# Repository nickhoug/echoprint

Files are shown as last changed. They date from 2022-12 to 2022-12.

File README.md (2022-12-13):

# EchoPrint

EchoPrint is an open-source Arduino-based hardware and software system to accompany the Creality3D Ender-3 or Ender-3 Pro 3D printers to enable 3D printing for visually disabled creators. 

The EchoPrint GitHub is designed for easy screenreader navigation of the creation and usage of the EchoPrint. It is meant to accompany the Ender-3's SainSmart 3D Printer User Guide and be used with a pre-built and set-up Ender-3 printer.

This system has two components: a screen reader for the built in LCD screen and 2. 3D-Printed printer and safety guards. To reproduce the system, please refer to Quick Start [Step 0] to get started.

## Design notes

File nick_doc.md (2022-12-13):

## Communication Protocol (I2C)

Echoprint uses a common communication protocol called I2C stands for "Inter-Integrated Circuit" and basically, the controller device (the printer) sends out an address that a device connected to the printer might have. In colloquial language, the printer is mailing out a message and is first seeing if the person is home. If there is a device on the connection lines that responds to the address, then it starts to listen to the incomming transmission. This allows us to hook more than one device upto these two data lines and allows further expansion of the printer.

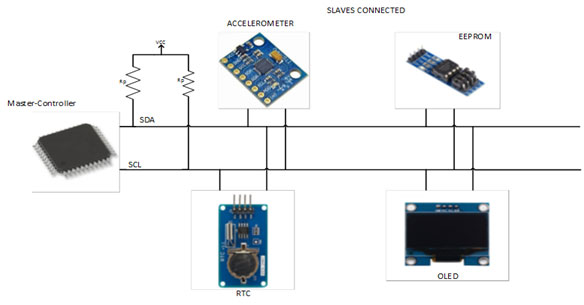
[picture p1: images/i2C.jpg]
I2C Protocol


## Text-To-Speech (tts)

The heart of this project uses Linear Predictive Coding (LPC), a speech model developed in the late 1980's and found in many kids toys at the time. If you've ever heard a dated robotic voice, it was most likely LPC that made it happen. At a high level, a model of human speech and all syllable sounds is convoluted with the input sound, thus making a computerized model of human speech. 

The  ["Talkie.h" library for Arduino ](https://github.com/ArminJo/Talkie)make use of this model and offer hundreds of vocabulary words preprogrammed into the library. The printer sends a command to Echoprint, and using a combination of the current command and the last sent command, Echoprint can determine what menu option the printer is highlighting. Once it knows the menu item in question, the specific word or set of words is sent to the speakers so the user can hear the item. 

There are some ways to preprogram your own words, and even a couple tools including BlueWizard for MacOS and the "python_wizard" available on the Talkie.h Github, but we found the preprogrammed words to be sufficient enough and expansion is definetly available in the future. 

## How to Install Echoprint

### 1. Remove the mainboard cover

Located on the bottom of the printer are three hex screws that utilize a size 2mm hex allen wrench. Remove these screws and gain acess to the main motherboard of the printer. Keep these screws somewhere save and when the cover comes off, there will be a fan cable attached to it, so disconnect it carefully. 

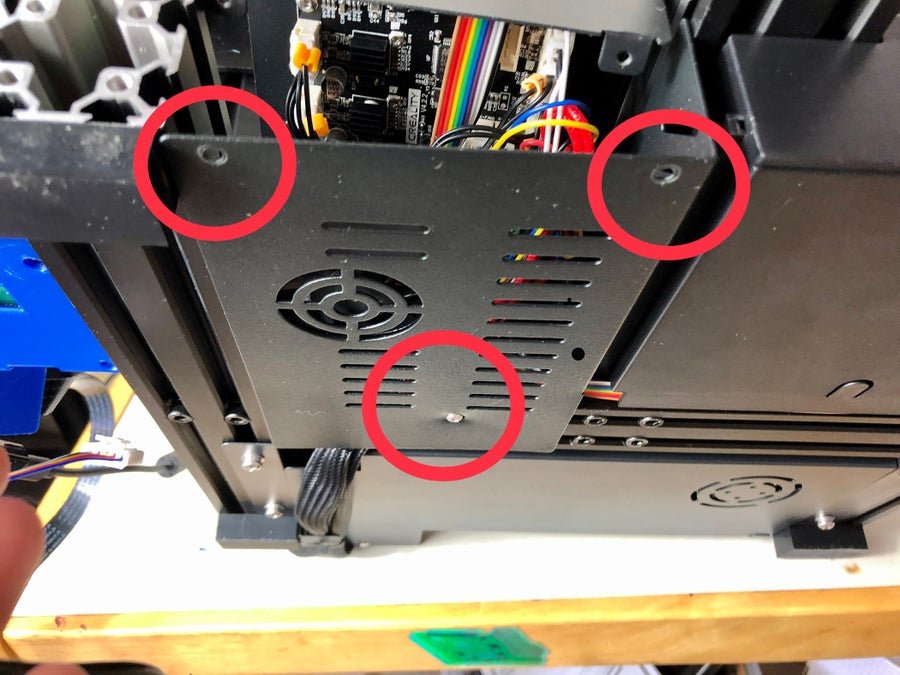
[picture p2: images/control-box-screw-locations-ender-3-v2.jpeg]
Mainboard Cover


### 2 Install the bootloader for the Creality Ender 3 Pro

Before any code can be flashed onto the printer, the bootloader needs to be installed first. This allows the printer to run any code put on to it and configures all of the internal settings. The best method for this is following along with the video below. This is a simple process that is necessary for programming the printer for a variety of applications, not just Echoprint. 

Hardware Required: 
- [AVR USB ISP Programmer](https://www.amazon.com/dp/B07NZ59VK2?psc=1&ref=ppx_yo2ov_dt_b_product_details)
- [3x2 6-pin Ribbon Cables](https://www.amazon.com/dp/B07Q2SX5CX?psc=1&ref=ppx_yo2ov_dt_b_product_details)

Video:  

IMAGE_ALT (https://www.youtube.com/watch?v=aquuSNEekvY)

### 3. Download the repository from the [Echoprint Github](https://github.com/nickhoug/echoprint)

This repository holds everything from documentation to the Ender 3 CAD files for all of the mechanical parts. Most importantly is the directory: 
    
    echoprint/Ender-3 Firmware (Marlin)/Ender-3 (includes power failure resume- English)/Marlin/Marlin.ino

This is the Arduino source code for the Ender 3 Pro and includes the Echoprint library files within the parent directory "Marlin", plus all of the instances of where the functions need to be called. Mainly, these functions are congregated in the "ultralcd.cpp" file. 

### 4. Remove the circuit board from the printer. 

Around and within the circuit board are 6 hex screws that utilize the same screwdriver as before. Remove these screws and keep them somewhere save - they are all the same size. 

After this is done, disconnect all of the connections to the printer. It's intuitive where they go and they are all labeled, but make sure to take lots of pictures as you go. The goal is to remove the board and prepare it for soldering, so we need access to the other side. 

### 5. Solder and splice the necesary connections onto the Ender 3 mainboard. 

Now that we have the software downloaded, we now need to establish an I2C connection. Through the use of Pin 27 and Pin 29 on the Ender 3 mainboard. The mainboard is very short of GPIO pins, so were going to have to hack it to make it work. 

First off is pin 27. This is a forgotton GPIO pin located under one of the boards main capacitors. The story behind this was that there was a connector for it to expand the printers hardware, but due to heating issues, this connector was removed and a capacitor was put in it's place. Located as shown in the picture below (this is from a dated source, and back then, it was still called pin 35). Make sure to cover with either heat shrink or electrical tape.

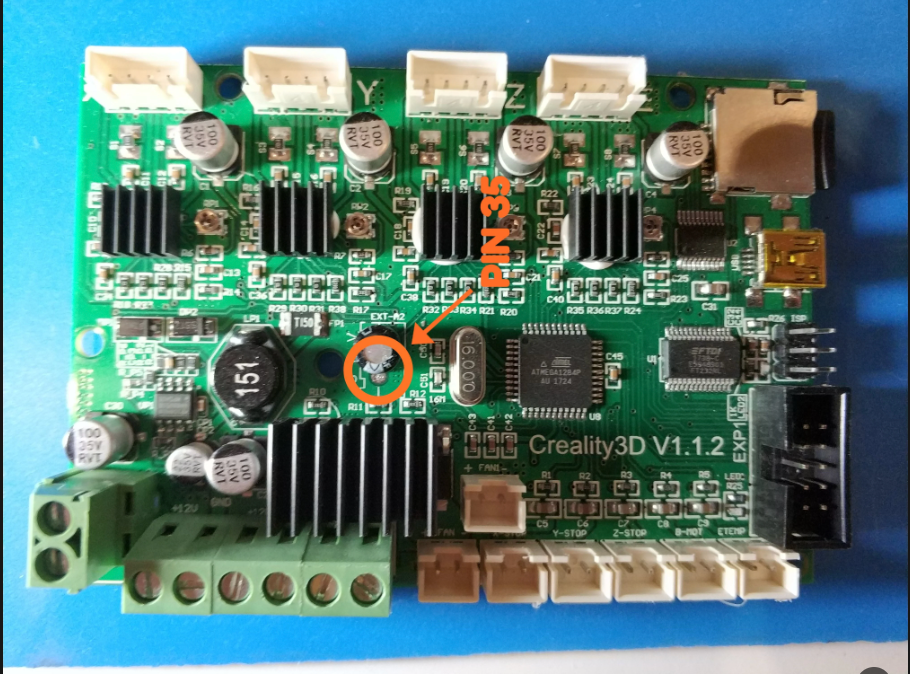
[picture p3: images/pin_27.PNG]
Pin 27


To get access to the pin, the solder needs to be removed from the hole and a jumper/wire needs to be resoldered in it's place. For the Echoprint application, a male jumper with a female end thats around 8 inches long is recommended.

Next up is pin 29. This pin is connected to the buzzer located on the LCD screen for the printer and to gain access, we need to splice into it using the rainbow ribbon connector on the printer. There are adapters made for this pin, but splicing into the wire works just as well. it is important to note that this will **remove buzzer functionality**. The engineering choice made here was that if exterrnal speakers were being added to the printer, the haptic feedback buzzer was worth ditching. On the rainbow LCD connector, the one that plugs into the black 2x5 connector near the USB port, cut the **brown** wire about an inch from the connection. Pull this wire away from the rest of the ribbon cable and solder another female jumper to it, again 8 inches in length. Again, make sure to cover with either heat shrink or electrical tape. 

### 6. Add power and ground lines 

Now that the data lines are established, we now need power and ground. In between the 2x5 LCD display connectopr and the USB is a 3x2 header pin connector. On the side closest to the edgeof the PCB and in the orientation as shown in the picture above, the pin closest to the USB port is the Ground pin and the pin closest to the LCD connector is the Power pin, skipping the one in the middle. Connect female-to-female jumpers to these pins and make sure the connections are about 8 inches long. 

### 7. Reinstallation

Once these two connections are made, reinstall the mainboard following the reverse steps as before and route the connections threw the small notch in the top plate; the plate the board is mounted to. Make sure to mount the bottom cover and fan back to the board and plugging it in the process. 

### 8. Mount Echoprint

Now that all of the electrical connections are made, we can start mounting the Echoprint system. Uncover the Echoprint system and locate the header pins. Using the schematic below, wire up all the connections, route it through the routing hole at the top of the box, and recover Echoprint. 

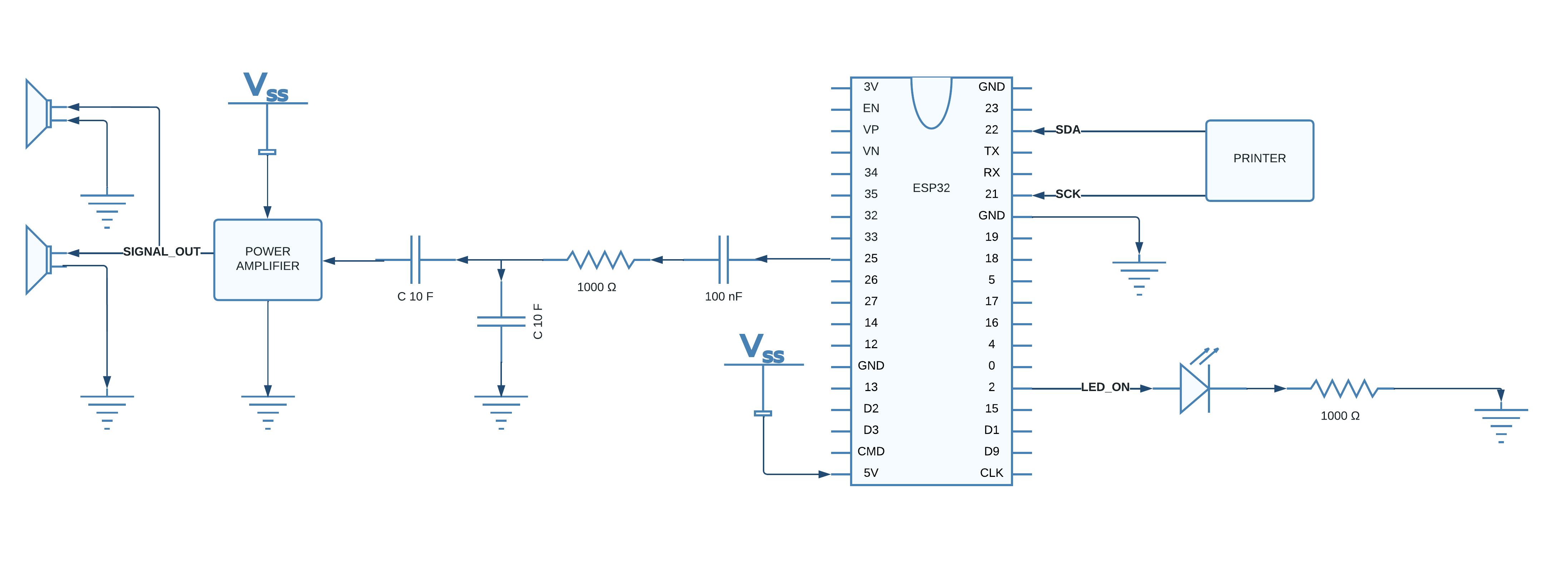
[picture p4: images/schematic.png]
Schematic


With the printer's LCD facing you, on the bottom right are 2 M4 screws. Unscrew these and thread them through the cooresponding holes on the Echoprint mount. Screw the screws back in to the holes they came out of and the Echoprint system is mounted. 

### 9. Finish

After this, Echoprint should power on with your printer and using 1980's text-to-speech technology, read out the LCD on the Ender 3 Pro. 

Given that the Creality Ender 3 system is an open-source system likely to experience updates in it's time, the following menu was used to program Echoprint and update files will be posted on the Github. 

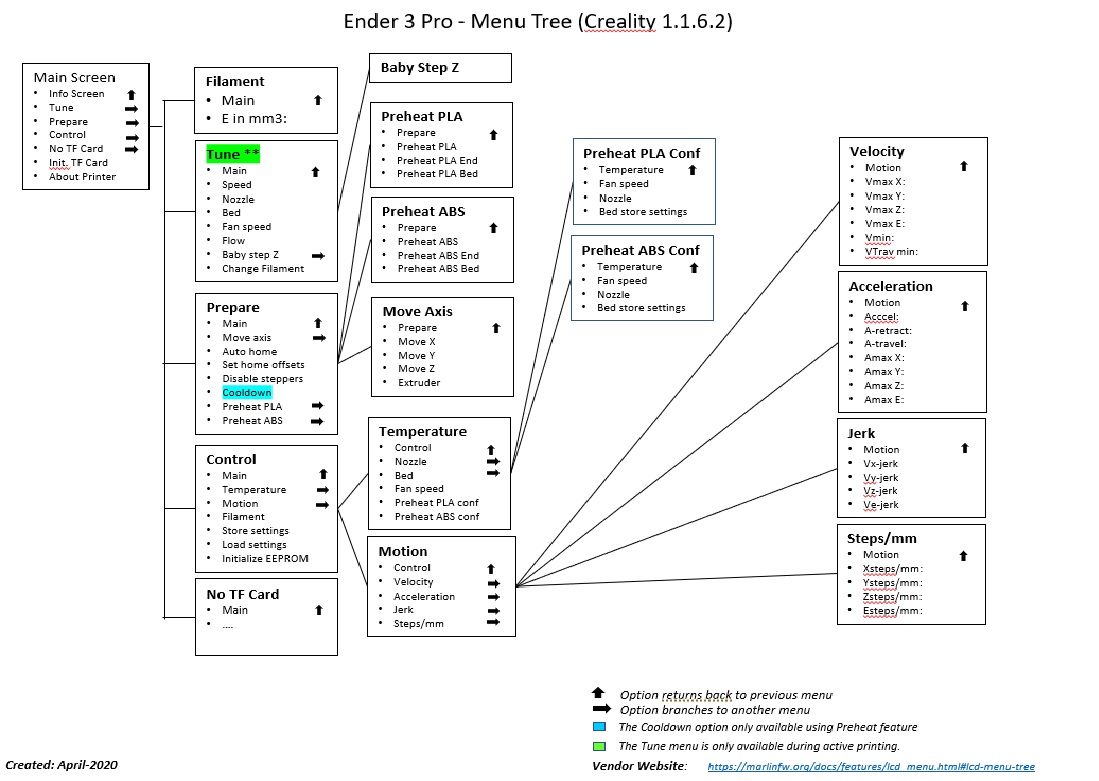
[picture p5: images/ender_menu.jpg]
Menu Tree


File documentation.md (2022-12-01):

# EchoPrint Documentation

## Abstract

EchoPrint is an Arduino-based hardware system for the Ender 3 and Ender 3 Pro 3D printers. This system is meant to act as a screen reader for the built in LCD screen on the printer. 
 
## How to Use 

## Features 

### Hardware/Firmware

## Things to do for documentation
- Make schematic 
- Outline how bigbanging system works
- List hardware pieces
- Talk about main problem and Lindsay? 
- Link Github 
- Make block diagram 
- Outline how to use the system
-

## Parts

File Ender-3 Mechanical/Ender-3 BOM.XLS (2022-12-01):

Ender-3 BOM
Part Code | Part Name | Specification | UNIT | Qty
200101027 | Control panel | 1284P | PCS | 1
200102010 | LCD |  | PCS | 1
400101002 | E plate | 2.5mm | PCS | 1
400101005 | Y Motor holder | 3mm | PCS | 1
400101006 | X Adjustment Block | 3mm | PCS | 1
400101027 | Z Stent | 3.0mm | PCS | 1
400101029 | Fan cover | 0.8mm | PCS | 1
400101081 | Support frame | 2.0mm | PCS | 1
400101103 | E motor bracket | 2.5mm，B1 | PCS | 1
400101104 | X motor bracket | 3mm，B1 | PCS | 1
400101130 | Sheetmetal enclosure bottom | 0.8MM | PCS | 1
400101131 | Sheetmetal enclosure top | 0.8MM | PCS | 1
400101133 | LCD support | 2MM | PCS | 1
400101007 | Y Adjustment Block | 3mm | PCS | 1
400101129 | Y plate | 4mm | PCS | 1
400102065 | 2020 Top Profile | 20*20-L330 | PCS | 1
400102066 | 2020 X Profile | 20*20-L345 | PCS | 1
400102067 | 2040 Y Profile | 20*40-L330 | PCS | 1
400102068 | 2040 Right Profile | 20*40-L400 | PCS | 1
400102069 | 2040 Left Profile | 20*40-L400 | PCS | 1
400102070 | 4040 Central Profile | 40*40-L250 | PCS | 1
400102071 | 4040 Left Profile | 40*40-L290 | PCS | 1
400102072 | 4040 Right Profile | 40*40-L290-2 | PCS | 1
400103001 | E gear | D11-40 | PCS | 1
400104004 | Heat block | 20*20*10 | PCS | 1
400105008 | Radiator | 12*20*27.8mm,2*M3 | PCS | 1
400106003 | nozzle | 0.4mm | PCS | 2
400107006 | Catheter | D7-M6-L28mm | PCS | 1
400108001 | Spacers for rollers | D8-d5-H-8.35mm | PCS | 11
400108002 | Eccentric column | D7.2-d5-H-8.35mm | PCS | 5
400201001 | 42-34 Motor | JK42HS34-0844YA-03F | PCS | 3
400201004 | 42-40 Motor | JK42HS40-1004AC-01F | PCS | 1
400202002 | 624U Pillow | 624U | PCS | 1
400202003 | F688ZZ Pillow | F688ZZ | PCS | 4
400202004 | 625ZZ Pillow | 625ZZ | PCS | 26
400204002 | Extrusion Spring | 1.1*8*L22 | PCS | 5
400205002 | M2*8 Socket Head Screw | M2*8 | PCS | 2
400205003 | M2*10 Socket Head Screw | M2*10 | PCS | 2
400205007 | M3*18 Socket Head Screw | M3*18 | PCS | 1
400205013 | M4*8Socket Head Screw | M4*8 | PCS | 7
400205014 | M4*10 Socket Head Screw | M4*10 | PCS | 2
400205015 | M4*16 Socket Head Screw | M4*16 | PCS | 4
400205018 | M3*3 screw | M3*3 | PCS | 4
400205019 | M4 screw | M4 | PCS | 4
400205021 | M3*4 Pan Head Screw | M3*4 | PCS | 1
400205029 | M3*6 Pan Head Screw | M3*6 | PCS | 18
400205031 | M3*10 Pan Head Screw | M3*10 | PCS | 12
400205032 | M3*16 Pan Head Screw | M3*16 | PCS | 5
400205044 | M5*8 Pan Head Screw | M5*8 | PCS | 8
400205053 | M5*30 Pan Head Screw | M5*30 | PCS | 10
400205055 | M5*40 Pan Head Screw | M5*40 | PCS | 3
400205060 | M3*10 Pan Head Screw | M3*10-P | PCS | 1
400205068 | M4*14 Pan Head Screw | M4*14-P | PCS | 2
400205074 | M4*35 Flush Head Screw | M4*35-P | PCS | 4
400205097 | M5 Self-locking nut | M5 | PCS | 13
400205098 | M8 Self-locking nut | M8 | PCS | 2
400205101 | M4 T-Slot Nut | M4T | PCS | 8
400205102 | M5 T-Slot Nut | M5T | PCS | 3
400205105 | M3 Split Washer | M3 | PCS | 6
400205106 | M4 Split Washer | M4 | PCS | 7
400205107 | M5 Split Washer | M5 | PCS | 12
400205109 | M5 washer | M5 | PCS | 5
400205110 | M5 washer1 | 5*8*1 | PCS | 13
400205111 | z nut | T8*8 | PCS | 1
400205122 | M4*20 Socket Head Screw | M4*20 | PCS | 3
400205140 | M4*18 Pan Head Screw | M4*18-P | PCS | 2
400205141 | M3*40 Pan Head Screw | M3*40-P | PCS | 4
400205144 | M3*18 Pan Head Screw | M3*18-P | PCS | 2
400205148 | M4*16 Screw |  | PCS | 5
400205153 | M3*6 Screw | M3*6 | PCS | 2
400205163 | M5*25 Socket Head Screw | M5*25 | PCS | 6
400205165 | M5*40 Socket Head Screw | M5*40 | PCS | 2
400205166 | M5*45 Socket Head Screw | M5*45 | PCS | 10
400205176 | M8*35 Pan Head Screw | M8*35 | PCS | 2
400206017 | Z threaded rod | T8*8-L365mm | PCS | 1
400208004 | Z coupler | D5*8 | PCS | 1
400210001 | Pneumatic joint | D4M8 | PCS | 1
400210002 | M6 Pneumatic joint | KJH04-06 | PCS | 2
400211009 | 2GT-pulley | 2GT-d5-20-6mm | PCS | 2
400212037 | X belt | 2M-W6-L786mm | PCS | 1
400212038 | Y belt | 2M-W6-L743mm | PCS | 1
400214001 | Copper cover | D8-0.8 | PCS | 4
400301008 | 24V15A power supply | 24V 15A | PCS | 1
400302026 | Hot bed | 24V，235*235mm，220W | PCS | 1
400303006 | Nozzle thermistor | D1.8-L1000mm-100K | PCS | 1
400303022 | Bed thermistor | D1.8-L700mm-100K | PCS | 1
400304001 | limit switch | 3PIN | PCS | 3
400305007 | power switch | 10A | PCS | 1
400306127 | Red silicone wire | 16号-L170mm | PCS | 1
400306128 | Yellow silicone wire | 18号-L170mm | PCS | 1
400306145 | Black silicone wire | 16号-L170mm | PCS | 1
400306217 | Hot bed line | 16号-L500mm | PCS | 1
400306221 | Red silicone wire | 16号-L90mm, | PCS | 1
400306222 | Main board line | 16号-L310mm,XT60 | PCS | 1
400306223 | power line | 16号-L170mm,XT60 | PCS | 1
400306224 | X,E Motor Line | Motor Line L670mm，Limit Line L750mm | PCS | 1
400306225 | Y Motor Line | L420mm | PCS | 1
400306226 | Z Motor Line | Motor LineL280mm，Limit Line L180mm | PCS | 1
400306228 | Display line | 10pin,L470mm | PCS | 1
400307001 | lcd Knob |  | PCS | 1
400308002 | Heater | 24V，40W-L1000MM，Φ6*20 | PCS | 1
400309032 | Cold section fan | 24V-4010-L1000-7600r | PCS | 1
400309044 | Nozzle fan | 24V-4010-L1000-5800r | PCS | 1
400309045 | Case fan | 24V-4010-L150mm | PCS | 1
400402010 | Z motor bracket |  | PCS | 1
400402020 | 2020 Endcap | 2020 | PCS | 2
400402023 | Nozzle fan duct |  | PCS | 1
400402028 | Power holder | 2mm | PCS | 1
400402032 | Y limit switch bracket | ABS | PCS | 1
400402033 | Z limit switch bracket | ABS | PCS | 1
400403003 | Rollers |  | PCS | 13
400403004 | Support tube |  | PCS | 1
400403005 | M30 Plastic nut | M30*6.5 | PCS | 2
400404030 | Hot bed wire bracket |  | PCS | 1
400404031 | Hot bed line support cover |  | PCS | 1
400404032 | E idler tensioner |  | PCS | 1
400404033 | E housing |  | PCS | 1
400404038 | X limit switch bracket | ABS | PCS | 1
400404040 | Hand Twisted Nut | D60mm | PCS | 4
400404041 | 4040 Endcap | ABS | PCS | 2
400406006 | Foot pads | 20*40mm*3mm | PCS | 4
400407013 | D4 Teflon tube | D4-d2-L400mm | PCS | 1
400409003 | Silk pole cover | T8*8 | PCS | 1
400501034 | Linear tube | W8-L450mm | PCS | 1
400501035 | Linear tube | W8-L950mm | PCS | 1
400504007 | Fan cover sticker |  | PCS | 1
400504008 | Product Qualification Certificate |  | PCS | 1
400505021 | Fiber board | 235*235*1.0mm | PCS | 1
400506001 | Scissor |  | PCS | 1
400506002 | shovel |  | PCS | 1
400506005 | 1.5# Hexagonal wrench inside |  | PCS | 1
400506006 | 2# Hexagonal wrench inside |  | PCS | 1
400506007 | 2.5# Hexagonal wrench inside |  | PCS | 1
400506008 | 3# Hexagonal wrench inside |  | PCS | 1
400506009 | 4# Hexagonal wrench inside |  | PCS | 1
400506011 | screwdriver |  | PCS | 1
400506016 | power cord |  | PCS | 1
400506020 | needle |  | PCS | 1
400506029 | tie | 4*150mm | PCS | 10
400506035 | 6# Open wrench |  | PCS | 1
400506036 | 8-10# Open wrench |  | PCS | 1
400506044 | Clip | 6#,15mm | PCS | 4
500101065 | Bubble cotton | 495*380*160mm | PCS | 1
500201001 | Self-Sealing bag | 6cm*9cm*0.8mm | PCS | 14
500201002 | Self-Sealing bag | 9cm*13cm*0.8mm | PCS | 1
500201004 | Self-Sealing bag | 15cm*20cm*0.8mm | PCS | 2
500201006 | Self-Sealing bag | 18cm*26cm*0.6mm | PCS | 1
500201008 | Prevention electrostatic bag | 15cm*20cm | PCS | 1
500301056 | paper box | 510*400*190mm | PCS | 1
500601001 | Opinion Card |  | PCS | 1
600101011 | Instruction |  | PCS | 1
600401004 | Memory Card | 8G | PCS | 1
600501001 | Card Reader |  | PCS | 1
600601016 | warranty card |  | PCS | 1
600601023 | Manufacture of numbered stickers | 60*10.4MM | PCS | 1
600601026 | Specification stickers | 65*40mm | PCS | 1
600601058 | Facebook code sticker | 41*41mm | PCS | 1
700206003 | Testing consumables | 5M | PCS | 1
700301044 | High temperature cotton | 20*50mm | PCS | 1
700301051 | gummed paper | 30*60 | PCS | 3
700301054 | gummed paper | 60*60mm | PCS | 1
700301056 | High temperature cotton | 50*60mm | PCS | 1

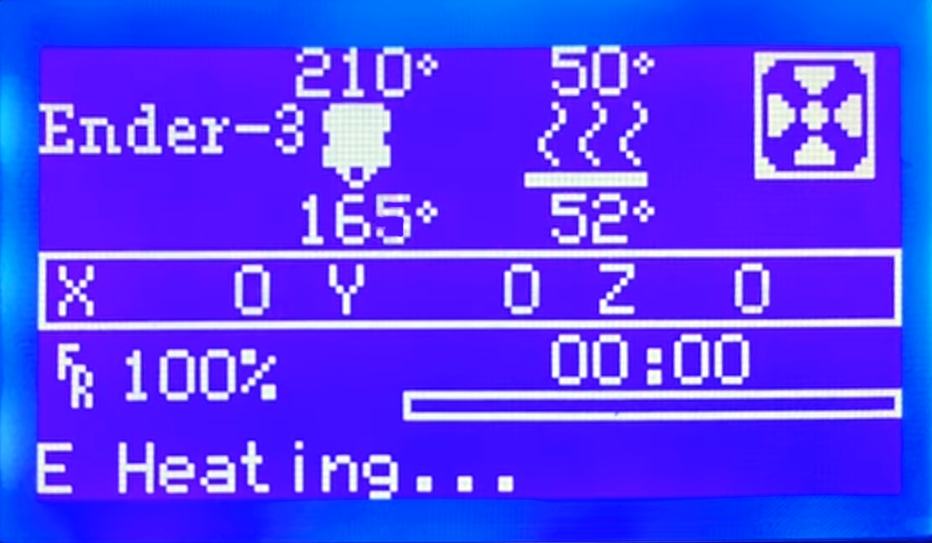
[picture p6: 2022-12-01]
Ender-3 Mechanical/Ender-3 Parts/ender_lcd.png

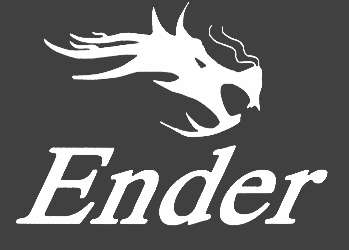
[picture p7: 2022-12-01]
Ender-3 Mechanical/Ender-3 Parts/ender-3.png

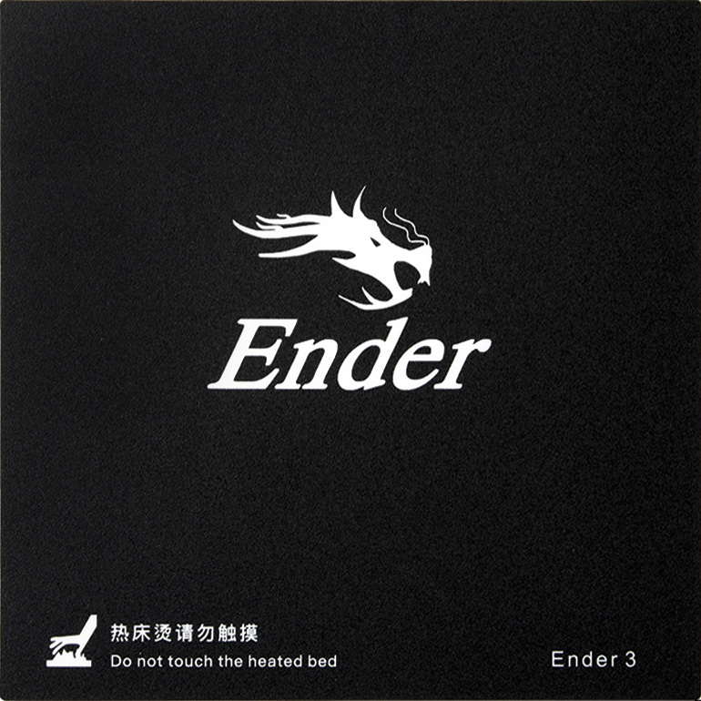
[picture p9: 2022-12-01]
Ender-3 Mechanical/Ender-3 Parts/ender-3.jpg

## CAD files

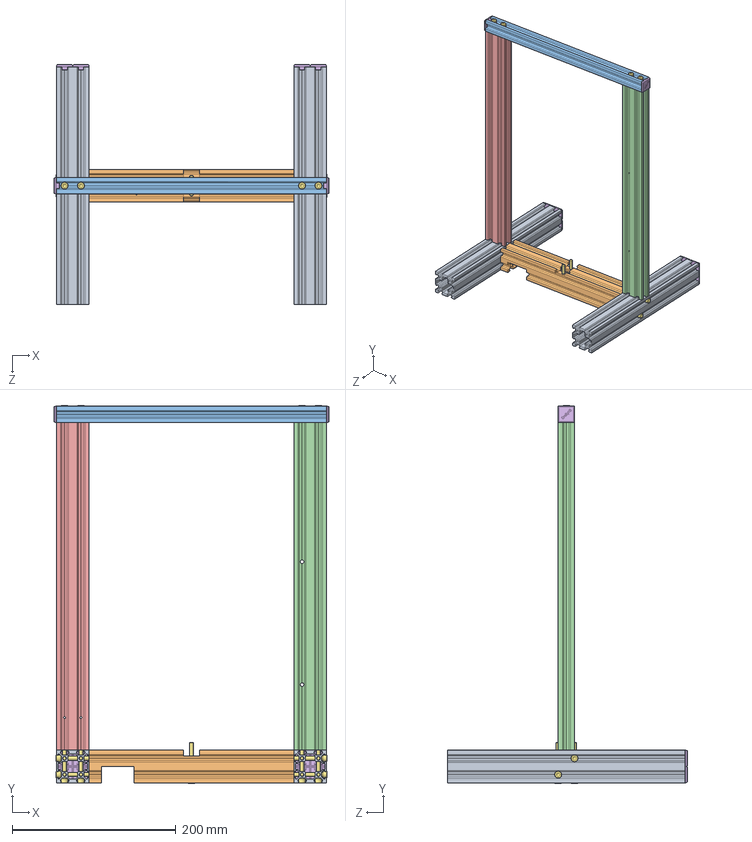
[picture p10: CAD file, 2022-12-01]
Ender-3 Mechanical/Ender-3 Parts/ASM Frame.SLDASM
335.7 x 461.6 x 292.9 mm
4040 profile x 2
4040-3 profile
2020-2 profile
2040-3R profile
2040-3L profile
2020 Endcap x 10
M5X45 Socket Head Screw x 14

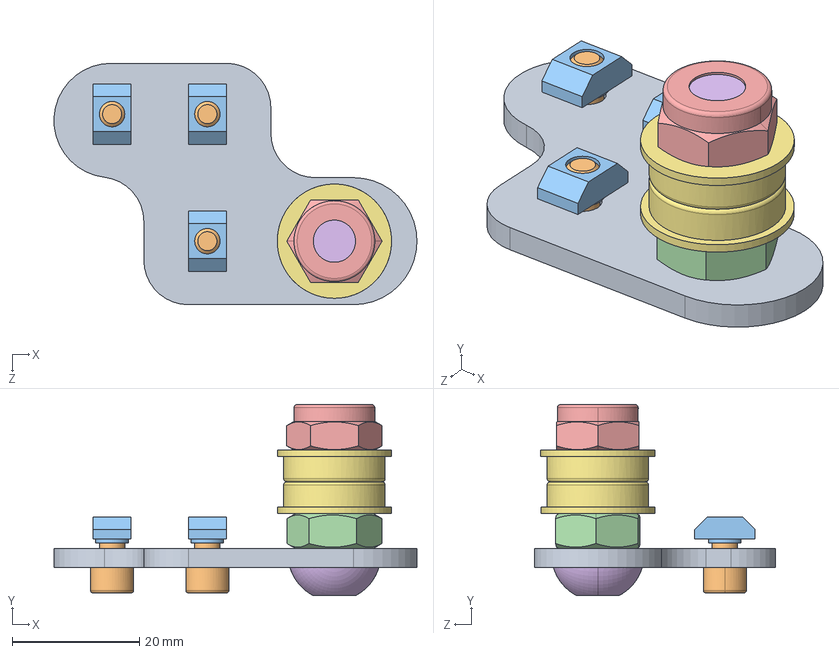
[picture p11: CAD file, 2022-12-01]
Ender-3 Mechanical/Ender-3 Parts/pulley mount.SLDASM
57.1 x 30.1 x 38.0 mm
Y Adjustment Block
M4X8 Socket Head Screw x 3
M4 T-Slot Nut x 3
M8 nut
M8 Self-locking nut
M8X25 Pan Head Screw
F688 pillow x 2

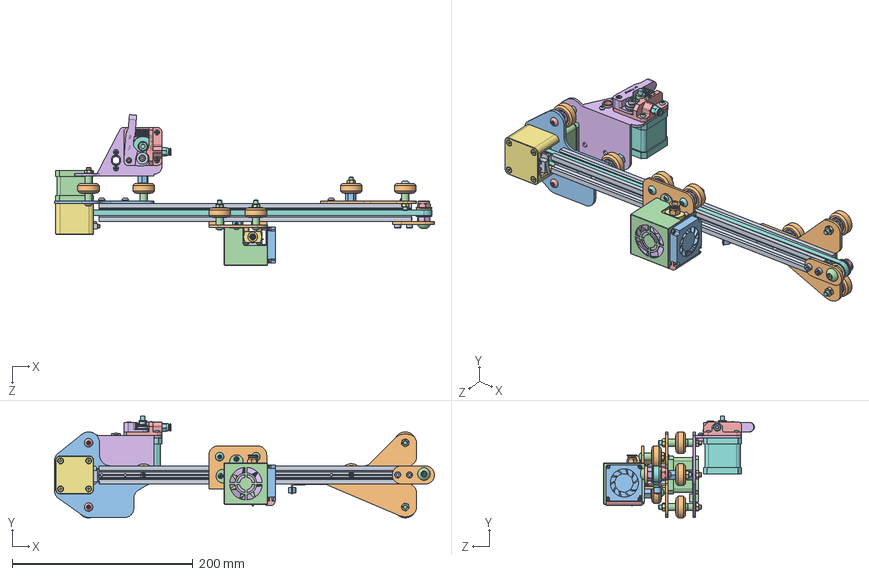
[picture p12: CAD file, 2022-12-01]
Ender-3 Mechanical/Ender-3 Parts/ASM X-Axis.SLDASM
420.0 x 112.6 x 166.7 mm
2020 profile
Z Stent
X motor bracket
42-34 motor
z nut
E motor bracket
X limit switch bracket
X belt
limit switch
2GT-pulley
Copper cover x 2
M4 Split Washer x 5
M3 Split Washer x 4
M4X16 Pan Head Screw x 4
M3X40-P x 4
M3X10 Pan Head Screw x 8
M3X6Pan Head Screw x 4
Rollers x 9
Eccentric column x 3
Spacers for rollers x 9
M5X40 Pan Head Screw x 3
625pillow x 18
M5 Self-locking nut x 9
40-42 motor
624U pillow
M3X18 Socket Head Screw
Extrusion Spring
E gear
E housing 2
E idler tensioner
M3X10 Flush Head Screw
M6 Pneumatic joint
M4X8 Socket Head Screw x 3
X Adjustment Block
M5 T-Slot Nut x 2
M8X25 Pan Head Screw
M8 Self-locking nut
M8 nut
F688 pillow x 2
M5X30 Pan Head Screw x 6
M5 Split Washer
E plate
Cold section fan
Fan cover
Nozzle fan duct
Nozzle fan
Radiator
nozzle
Heat block
Pneumatic joint
Nozzle thermistor
Heater
M3X16 Pan Head Screw x 2
M3×18 Flush Head Screw x 2
M3 Screw x 2
M5 washer
M2X8 Socket Head Screw x 4

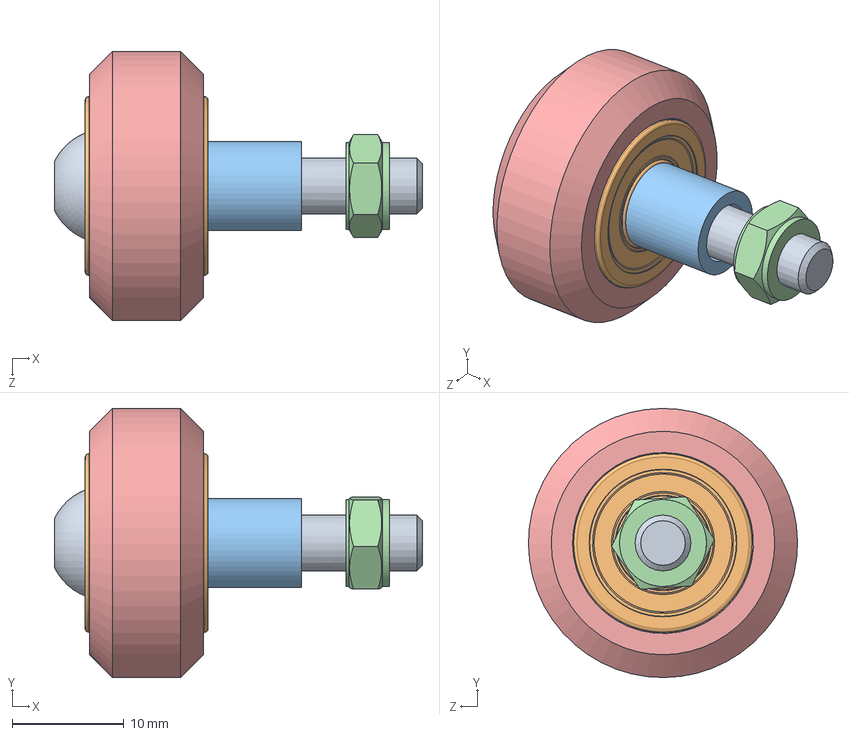
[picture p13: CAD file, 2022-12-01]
Ender-3 Mechanical/Ender-3 Parts/ASM Roller Y-Axis.SLDASM
33.0 x 24.1 x 24.1 mm
M5X30 Pan Head Screw
625pillow x 2
Spacers for rollers
M5 Self-locking nut
Rollers

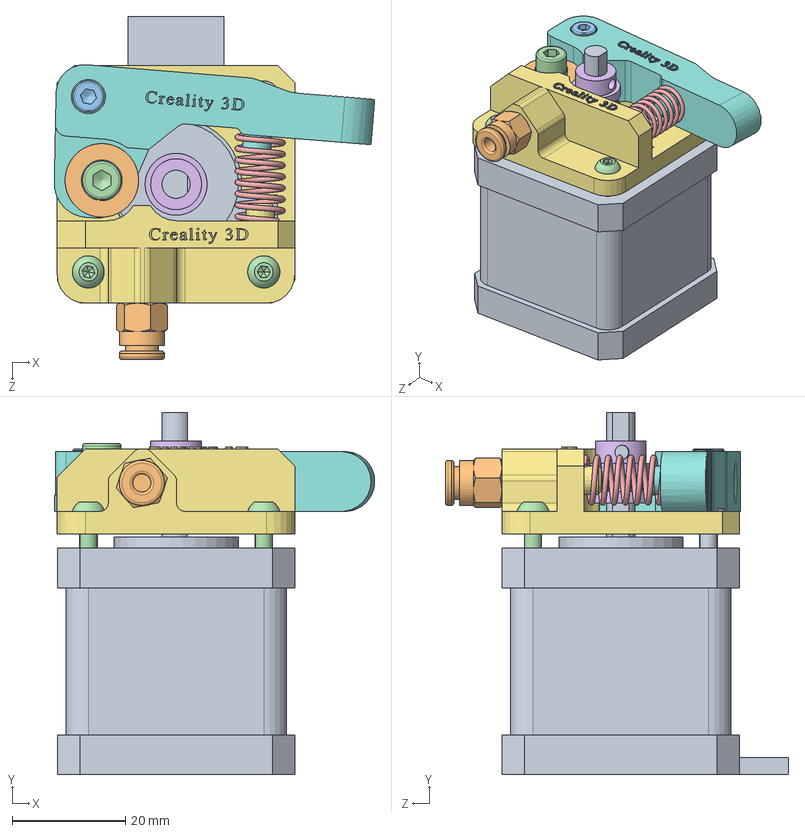
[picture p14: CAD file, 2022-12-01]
Ender-3 Mechanical/Ender-3 Parts/ASM Extruder.SLDASM
56.7 x 64.0 x 60.7 mm
40-42 motor
624U pillow
M3X18 Socket Head Screw
M3X10 Pan Head Screw x 2
Extrusion Spring
E gear
E housing 2
E idler tensioner
M3X10 Flush Head Screw
M6 Pneumatic joint
M4 Split Washer
M4X8 Socket Head Screw

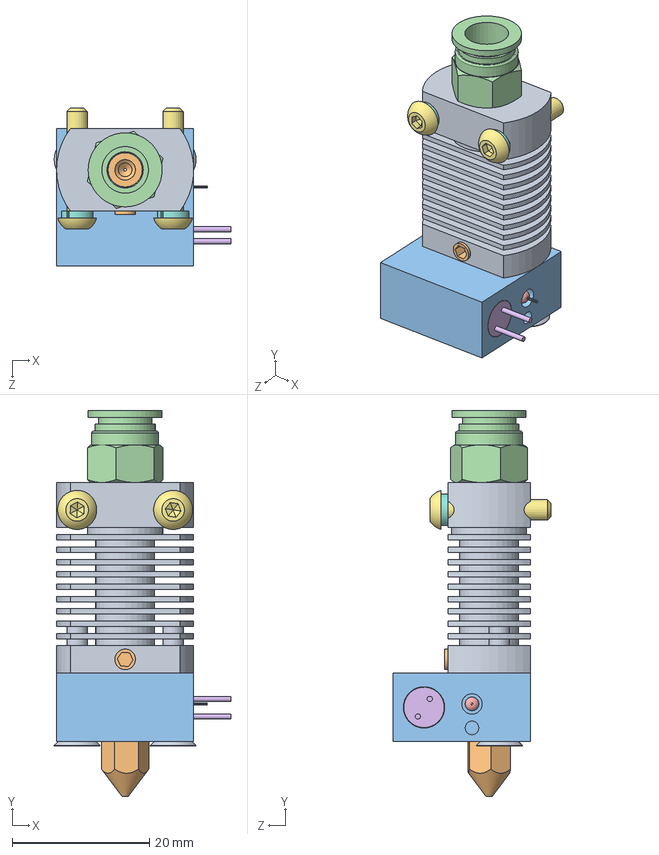
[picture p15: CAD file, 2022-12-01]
Ender-3 Mechanical/Ender-3 Parts/ASM Heating Unit.SLDASM
25.8 x 56.3 x 23.0 mm
Radiator
nozzle
Heat block
Pneumatic joint
Nozzle thermistor
Heater
M3X16 Pan Head Screw x 2
M3 Split Washer x 2
M3×18 Flush Head Screw x 2
M3 Screw x 2

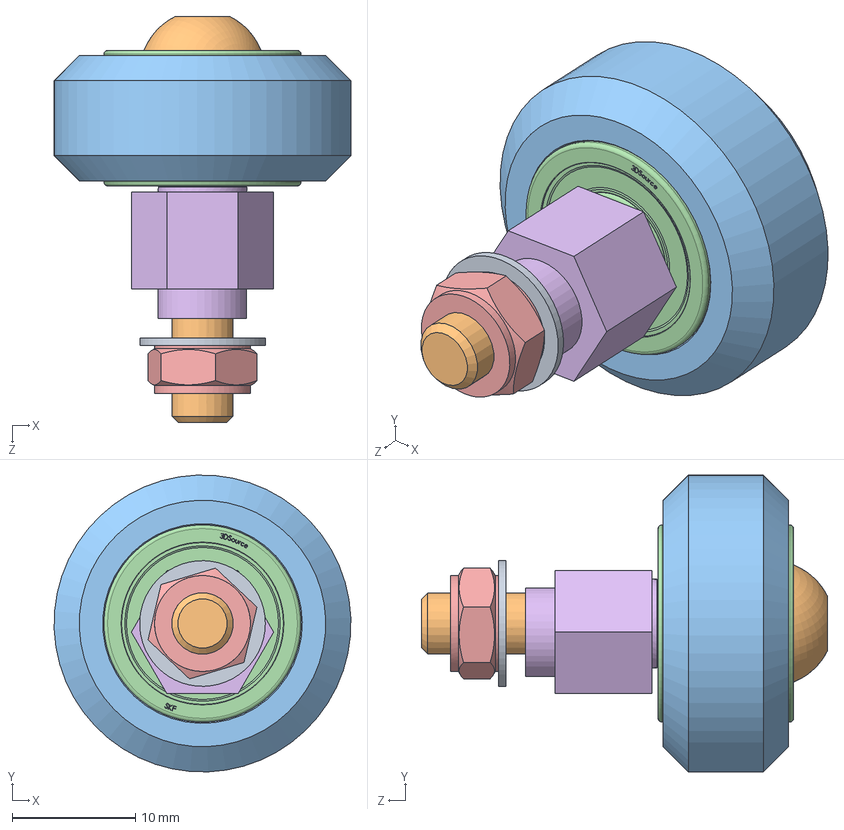
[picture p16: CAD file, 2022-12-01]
Ender-3 Mechanical/Ender-3 Parts/ASM Eccentrical Roller Y-Axis.SLDASM
24.1 x 24.1 x 33.0 mm
M5 washer
M5X30 Pan Head Screw
Rollers
625pillow x 2
M5 Self-locking nut
Eccentric column

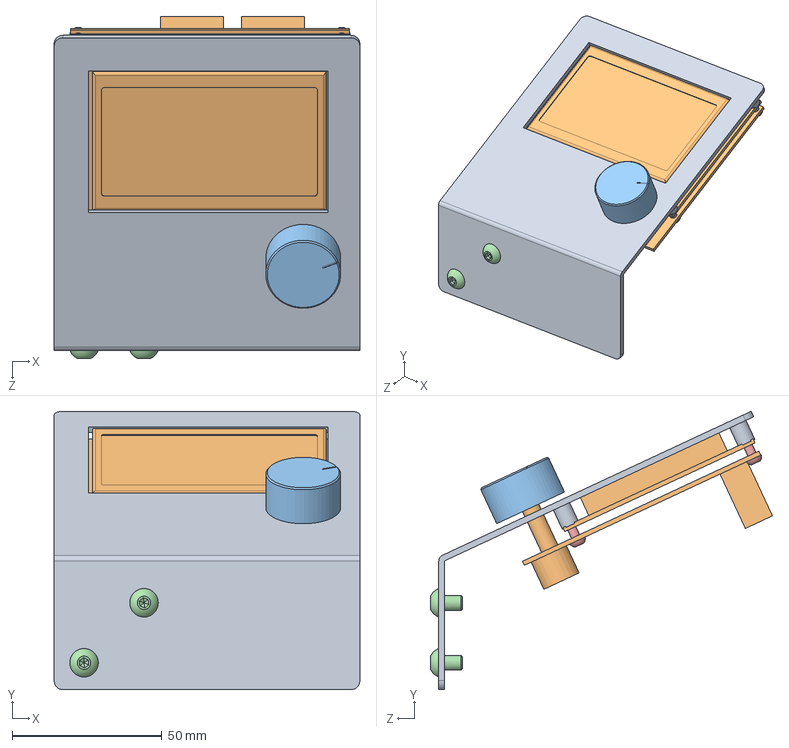
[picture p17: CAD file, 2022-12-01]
Ender-3 Mechanical/Ender-3 Parts/ASM Display.SLDASM
102.0 x 92.9 x 114.1 mm
LCD support
lcd
lcd Knob
M5X8Pan Head Screw x 2
M3X8 Pan Head Screw x 4

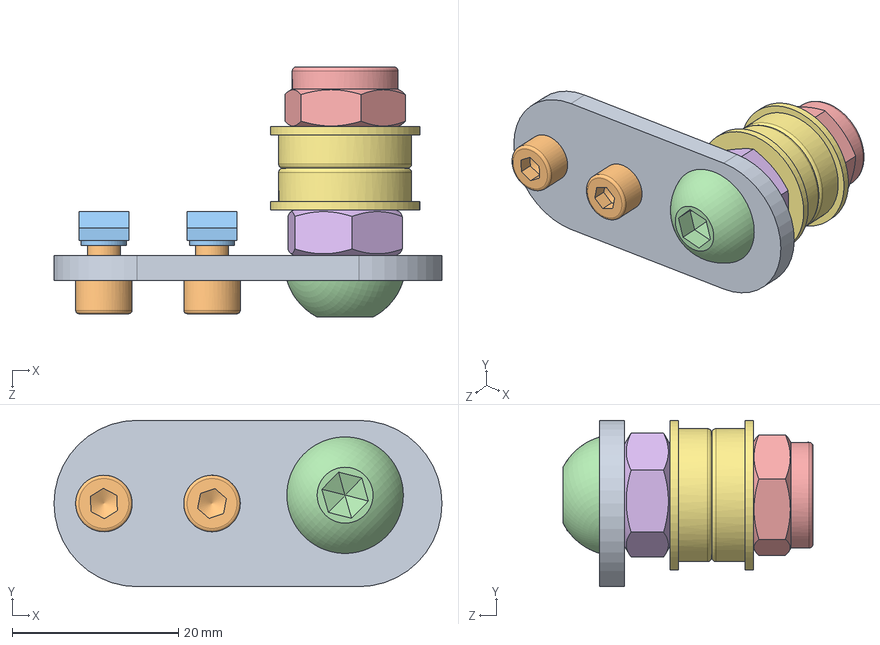
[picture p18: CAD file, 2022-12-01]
Ender-3 Mechanical/Ender-3 Parts/ASM X-Belt Tensioner.SLDASM
46.7 x 20.0 x 30.1 mm
X Adjustment Block
M4X8 Socket Head Screw x 2
M5 T-Slot Nut x 2
M8X25 Pan Head Screw
M8 Self-locking nut
M8 nut
F688 pillow x 2

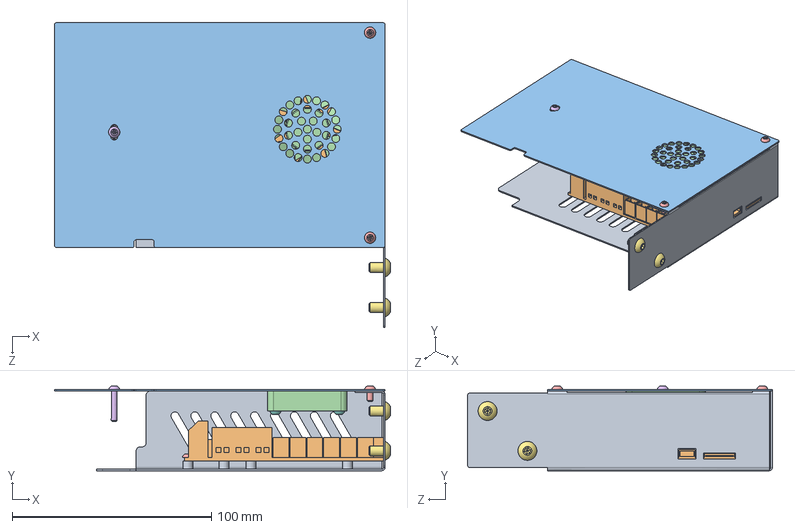
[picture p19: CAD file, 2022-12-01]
Ender-3 Mechanical/Ender-3 Parts/ASM Electronic Enclosure.SLDASM
168.8 x 42.5 x 153.0 mm
Sheetmetal enclosure bottom
Control panel
Sheetmetal enclosure top
Case fan
M3X6Pan Head Screw x 6
M3X16 Pan Head Screw
M5X8Pan Head Screw x 2
M3X10 Pan Head Screw x 2

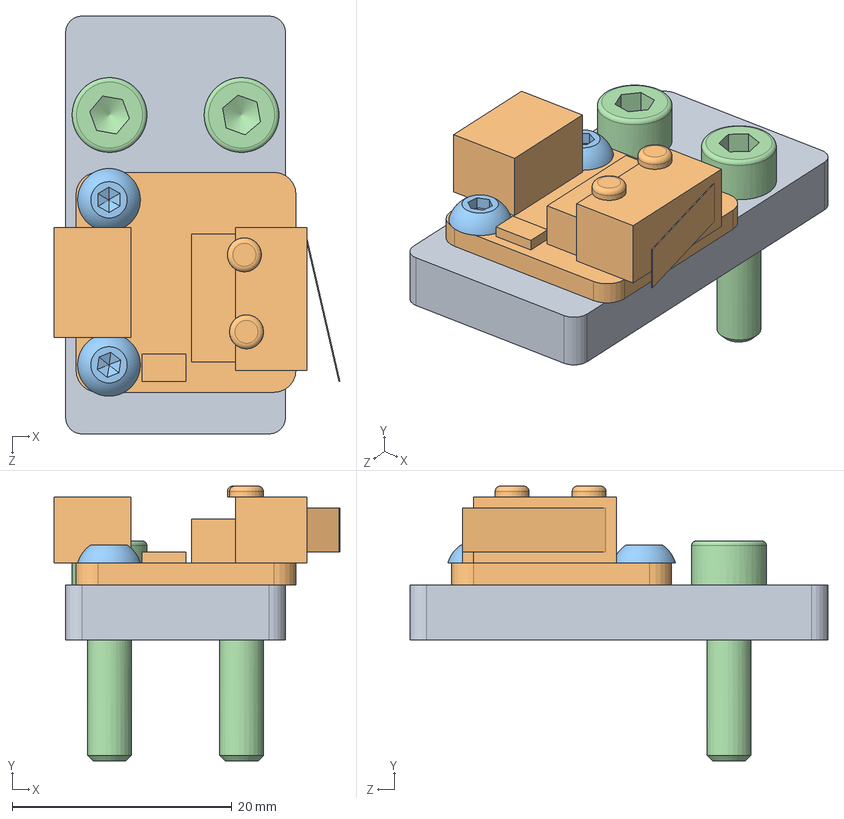
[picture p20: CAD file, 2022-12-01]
Ender-3 Mechanical/Ender-3 Parts/ASM Y-Axis Limit Switch.SLDASM
26.0 x 25.0 x 38.0 mm
Y limit switch bracket
limit switch
M3X6Pan Head Screw x 2
M4X16 Screw x 2

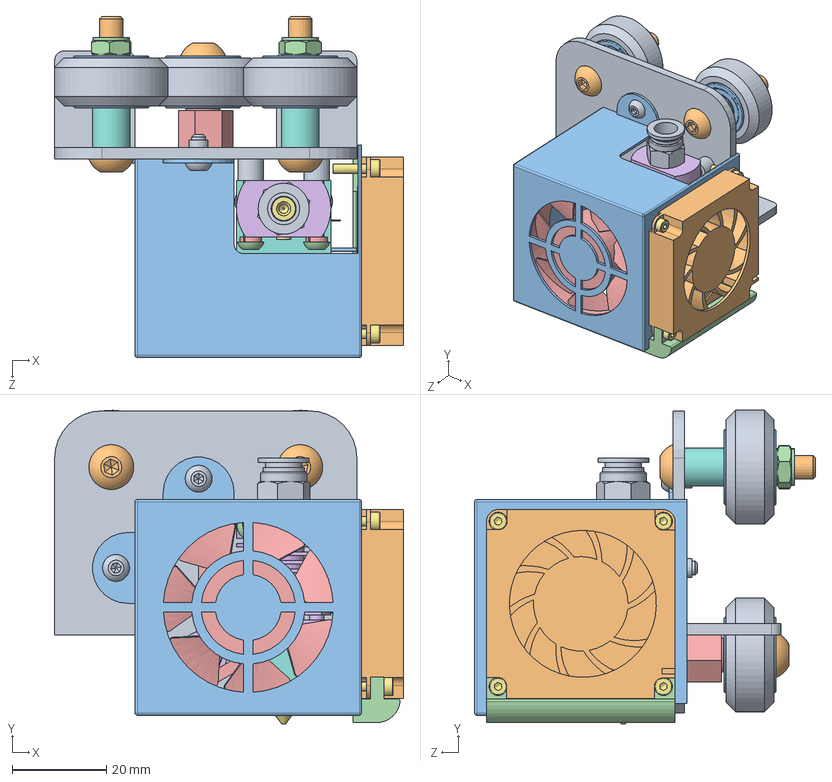
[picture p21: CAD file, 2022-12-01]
Ender-3 Mechanical/Ender-3 Parts/ASM Printing Head.SLDASM
73.9 x 66.4 x 72.2 mm
E plate
Cold section fan
Fan cover
Nozzle fan duct
Nozzle fan
Radiator
nozzle
Heat block
Pneumatic joint
Nozzle thermistor
Heater
M3X16 Pan Head Screw x 2
M3 Split Washer x 2
M3×18 Flush Head Screw x 2
M3 Screw x 2
Spacers for rollers x 2
Rollers x 3
M5X30 Pan Head Screw x 3
625pillow x 6
M5 Self-locking nut x 3
Eccentric column
M5 washer
M2X8 Socket Head Screw x 4
M3X10 Pan Head Screw x 4
M3X6Pan Head Screw x 2

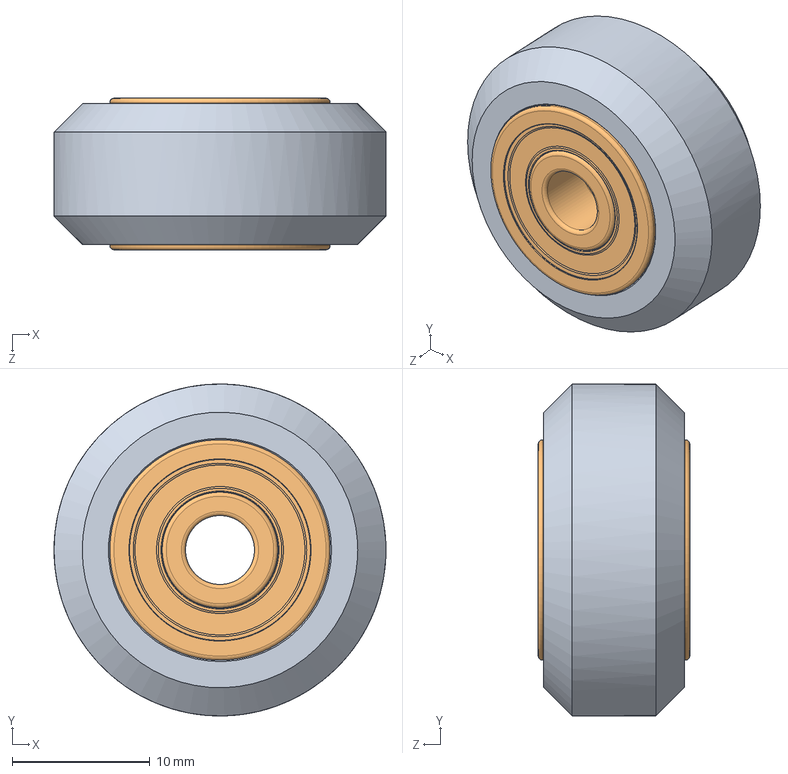
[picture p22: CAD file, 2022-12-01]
Ender-3 Mechanical/Ender-3 Parts/V Wheel Component.SLDASM
24.1 x 24.1 x 11.0 mm
Rollers
625pillow x 2

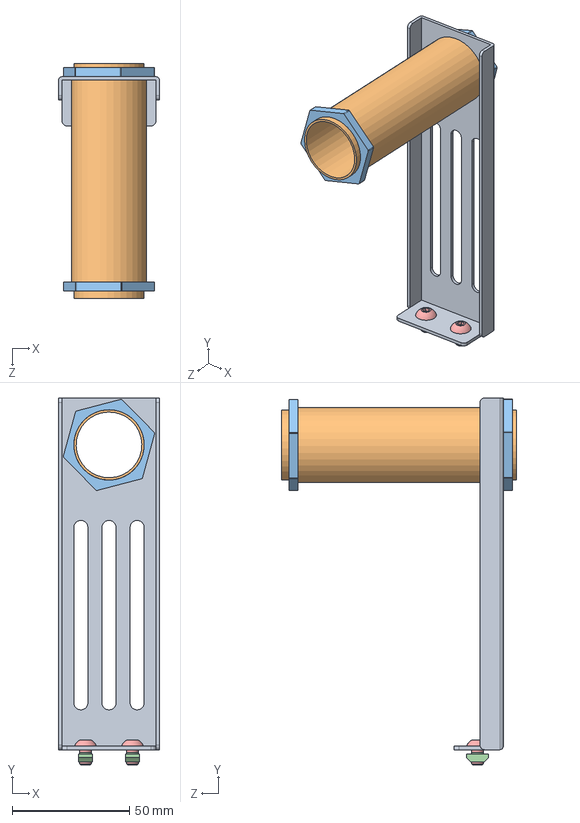
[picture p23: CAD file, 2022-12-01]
Ender-3 Mechanical/Ender-3 Parts/ASM Spool Holder.SLDASM
43.0 x 156.5 x 100.0 mm
Support frame
Support tube
M30 Plastic nut x 2
M4 T-Slot Nut x 2
M5X8Pan Head Screw x 2

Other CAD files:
Ender-3 Mechanical/Ender-3 Parts/ASM Roller X-Axis.SLDASM
Ender-3 Mechanical/Ender-3 Parts/ASM Y-Belt Tensioner.SLDASM
Ender-3 Mechanical/Ender-3 Parts/ASM Z-Axis Limit Switch.SLDASM
Ender-3 Mechanical/Ender-3 Parts/ASM Roller Z-Axis Right.SLDASM
CAD files/AXIAL_FAN_COVER.SLDPRT
CAD files/AXIAL_FAN_COVER.STL
CAD files/Board_Box.SLDPRT
CAD files/Board_Box.STL
CAD files/Board_Box_Lid.SLDPRT
CAD files/Board_Box_Lid.STL
CAD files/SIDE_FAN_COVER.f3d
CAD files/SIDE_FAN_COVER.stl
Ender-3 Mechanical/DWG/2020 Endcap.dwg
Ender-3 Mechanical/DWG/2020 profile_1.dwg
Ender-3 Mechanical/DWG/2020 profile_2.dwg
Ender-3 Mechanical/DWG/2040 profile_1.dwg
Ender-3 Mechanical/DWG/2040 profile_2.dwg
Ender-3 Mechanical/DWG/2040 profile_3.dwg
Ender-3 Mechanical/DWG/4040 profile_1.dwg
Ender-3 Mechanical/DWG/4040 profile_2.dwg
Ender-3 Mechanical/DWG/4040 profile_3.dwg
Ender-3 Mechanical/DWG/Catheter.dwg
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

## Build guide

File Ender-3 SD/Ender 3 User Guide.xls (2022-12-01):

Ender 3 User Guide
In order to open and read the files can help you finish it better.
1.Installing
Machine installation | Quick Start Guide
Machine installation（video）
2.USB Driver & Software
Cura-3.0.2-win64 | CURA 15 User Guide
Reference Data | Cura_15.04.3
Software Drivers | Online Printing
3.Trouble Shootings
Trouble Shootings
4.Modle
Test Modle | stl Files
5.visit website
About Us (http://www.creality3d.cn)
Modle Download (http://www.cxsw3d.com/moxingxiazai.html) | Cura Download (https://ultimaker.com/en/products/ultimaker-cura-software)

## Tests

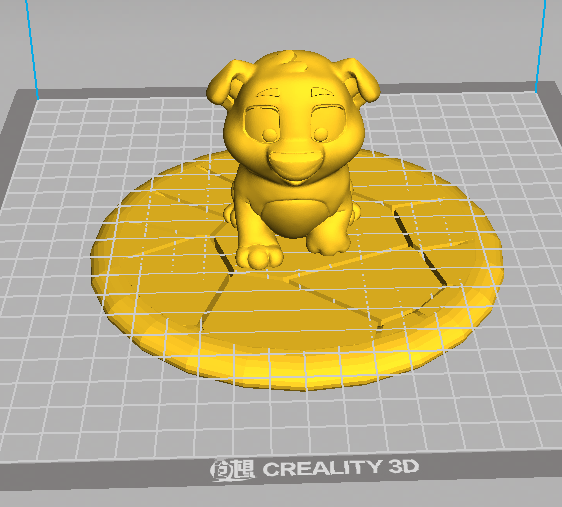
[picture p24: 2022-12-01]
Ender-3 SD/4.Modle/test/test-dog.png

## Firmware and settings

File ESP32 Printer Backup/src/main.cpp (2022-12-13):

#include "Wire.h"
#include "Arduino.h"
#include "Talkie.h" 
#include "Vocab_US_Large.h"
#include "Vocab_US_TI99.h"

#define IDLE 0
#define DOWN 1
#define UP 2
#define PRESSED 3

#define MAIN_MENU 0
#define TUNE 2
#define PREPARE 3
#define CONTROL 4
#define NO_TF_CARD 5
#define BABY_STEP_Z 6
#define PREHEAT_PLA 7
#define PREHEAT_ABS 8
#define MOVE_AXIS 9
#define TEMPERATURE 10
#define MOTION 11
#define PREHEAT_PLA_CONFIG 12
#define PREHEAT_ABS_CONFIG 13
#define VELOCITY 14
#define ACCELERATION 15
#define JERK 16
#define STEPS 17

Talkie voice;
uint32_t i = 0;
byte transmission; 
uint8_t screen_flag = 0; 
uint8_t sel_flag = 0; 
uint8_t next_state; 

const int buttonTop = 27;
const int buttonSel = 14;
const int buttonBot = 13;

int top_state; 
int buttonStateTop;
int buttonStateTop_old;
int buttonTopFlag; 

int sel_state; 
int buttonStateSel;
int buttonStateSel_old;
int buttonSelFlag; 

int bot_state; 
int buttonStateBot;
int buttonStateBot_old;
int buttonBotFlag; 

byte encoderLine = 0; 

void state_machine_top(int button_input) {
  buttonStateTop_old = buttonStateTop; 
  buttonStateTop = button_input;
  switch(top_state){
    case IDLE: 
      if (buttonStateTop_old == 1 && buttonStateTop == 0) {
        top_state = DOWN; 
      }
      break; 
    case DOWN: 
      if (buttonStateTop_old == 0 && buttonStateTop == 1) {
        top_state = UP; 
      }
      break; 
    case UP:
      buttonTopFlag = 1; 
      top_state = PRESSED;
      break; 
    case PRESSED:
      buttonTopFlag = 0; 
      top_state = IDLE; 
      break; 
  }
}

void state_machine_sel(int button_input) {
  buttonStateSel_old = buttonStateSel; 
  buttonStateSel = button_input;
  switch(sel_state){
    case IDLE: 
      if (buttonStateSel_old == 1 && buttonStateSel == 0) {
        sel_state = DOWN; 
      }
      break; 
    case DOWN: 
      if (buttonStateSel_old == 0 && buttonStateSel == 1) {
        sel_state = UP; 
      }
      break; 
    case UP:
      buttonSelFlag = 1; 
      sel_state = PRESSED;
      break; 
    case PRESSED:
      buttonSelFlag = 0; 
      sel_state = IDLE; 
      break; 
  }
}

void state_machine_bot(int button_input) {
  buttonStateBot_old = buttonStateBot; 
  buttonStateBot = button_input;
  switch(bot_state){
    case IDLE: 
      if (buttonStateBot_old == 1 && buttonStateBot == 0) {
        bot_state = DOWN; 
      }
      break; 
    case DOWN: 
      if (buttonStateBot_old == 0 && buttonStateBot == 1) {
        bot_state = UP; 
      }
      break; 
    case UP:
      buttonBotFlag = 1; 
      bot_state = PRESSED;
      break; 
    case PRESSED:
      buttonBotFlag = 0; 
      bot_state = IDLE; 
      break; 
  }
}

void state_machine(byte transmission, uint8_t screen_flag) {
  Serial.print(screen_flag);
  Serial.print("\n");
  switch(screen_flag) {
    case MAIN_MENU: 

      if (transmission == 0x00) {      //info screen
        voice.say(sp4_INFORMATION); 
        next_state = MAIN_MENU;
      }
      else if (transmission == 0x01) { //tune
        voice.say(sp2_ADJUST);
        next_state = TUNE;
      }
      else if (transmission == 0x02) { // prepare
        voice.say(spt_MAKE);
        voice.say(sp4_READY);
        next_state = PREPARE; 
      }
      else if (transmission == 0x03) { // control
        voice.say(sp4_CONTROL); 
        next_state = CONTROL; 
      }
      else if (transmission == 0x04) { // No TF card
        voice.say(sp4_NO);
        voice.say(sp2_S);
        voice.say(sp2_D);
        next_state = NO_TF_CARD; 
      }
      else if (transmission == 0x05) { // init TF card
        voice.say(sp4_START);
        voice.say(sp2_S);
        voice.say(sp2_D);
        next_state = MAIN_MENU;
      }
      else if (transmission == 0x06) { // About printer
        voice.say(sp2_ABOUT); 
        voice.say(spt_PRINTER); 
        next_state = MAIN_MENU;
      }

    break; 

    case TUNE: 

      if (transmission == 0x00) {      //info screen
        voice.say(sp4_INFORMATION); 
        next_state = MAIN_MENU;
      }
      else if (transmission == 0x01) { //speed
        voice.say(sp4_SPEED);
        next_state = TUNE;
      }
      else if (transmission == 0x02) { // Nozzle
        next_state = TUNE;
      }
      else if (transmission == 0x03) { // Bed
        next_state = TUNE;
      }
      else if (transmission == 0x04) { // Fan Speed
        next_state = TUNE;
      }
      else if (transmission == 0x05) { // Flow
        voice.say(sp2_FLOW);
        next_state = TUNE;
      }
      else if (transmission == 0x06) { // Baby step Z
        voice.say(spt_STEP);
        voice.say(sp2_Z);
        next_state = BABY_STEP_Z;
      }
      else if (transmission == 0x07) { // Change Filament
        voice.say(sp2_CHANGE); 
        next_state = TUNE;
      }

    break; 

    case BABY_STEP_Z: 
      if (transmission == 0x00) { // Baby step Z
        voice.say(spt_STEP);
        voice.say(sp2_Z);
        next_state = TUNE;
      }
    break; 

    case PREPARE:

      if (transmission == 0x00) {      //info screen
        voice.say(sp4_INFORMATION); 
        next_state = MAIN_MENU;
      }
      else if (transmission == 0x01) { //move axis
        voice.say(spt_MOVE); 
        voice.say(spt_PRINTER);
        next_state = MOVE_AXIS;
      }
      else if (transmission == 0x02) { // auto home
        voice.say(sp2_AUTOMATIC); 
        voice.say(spt_HOME);
        next_state = PREPARE;
      }
      else if (transmission == 0x03) { // Set home offsets
        voice.say(sp2_SET);
        voice.say(spt_HOME);
        voice.say(spt_OFF);
        voice.say(spt_SET);
        next_state = PREPARE;
      }
      else if (transmission == 0x04) { // Disable stepers
        voice.say(spt_END);
        voice.say(sp2_MOTOR);
        next_state = PREPARE;
      }
      else if (transmission == 0x05) { // Cooldown
        next_state = PREPARE;
      }
      else if (transmission == 0x06) { // Preheat PLA
        voice.say(sp3_HEAT);
        voice.say(sp2_P);
        voice.say(sp2_L);
        voice.say(sp2_A);
        next_state = PREHEAT_PLA;
      }
      else if (transmission == 0x07) { // Preheat ABS
        voice.say(sp3_HEAT);
        voice.say(sp2_A);
        voice.say(sp2_B);
        voice.say(sp2_S);
        next_state = PREHEAT_ABS;
      }

    break;

    case MOVE_AXIS:
      if (transmission == 0x00) {      //Prepare
        voice.say(spt_MAKE);
        voice.say(sp4_READY); 
        next_state = PREPARE;
      }
      else if (transmission == 0x01) { //Move X
        voice.say(spt_MOVE); 
        voice.say(sp2_X);
        next_state = MOVE_AXIS;
      }
      else if (transmission == 0x02) { // Move Y
        voice.say(spt_MOVE); 
        voice.say(sp2_Y);
        next_state = MOVE_AXIS;
      }
      else if (transmission == 0x03) { // Move Z
        voice.say(spt_MOVE); 
        voice.say(sp2_Z);
        next_state = MOVE_AXIS;
      }
      else if (transmission == 0x04) { // Move E (extruder)
        voice.say(spt_MOVE); 
        voice.say(sp2_E);
        next_state = MOVE_AXIS;
      }

    break;

    case CONTROL: 
      if (transmission == 0x00) {      //info screen
        voice.say(sp4_INFORMATION); 
        next_state = MAIN_MENU;
      }
      else if (transmission == 0x01) { //Temperature
        voice.say(sp3_TEMPERATURE);
        next_state = TEMPERATURE;
      }
      else if (transmission == 0x02) { // Motion
        voice.say(spt_MOVE);
        next_state = MOTION; 
      }
      else if (transmission == 0x03) { // Filament
        next_state = CONTROL;
      }
      else if (transmission == 0x04) { // Store Settings
        voice.say(spt_SAVE);
        next_state = CONTROL;
      }
      else if (transmission == 0x05) { // Load Settings
        voice.say(spt_LOAD); 
        next_state = CONTROL;
      }
      else if (transmission == 0x06) { // Initialize EEPROM
        voice.say(sp2_E);
        voice.say(sp2_E);
        voice.say(sp2_P);
        voice.say(sp2_R);
        voice.say(sp2_O);
        voice.say(sp2_M);
        next_state = CONTROL;
      }
      
    break;

    case TEMPERATURE: 
      if (transmission == 0x00) {      //control
        voice.say(sp4_CONTROL); 
        next_state = CONTROL; 
      }
      else if (transmission == 0x01) { //nozzle
        next_state = TEMPERATURE; 
      }
      else if (transmission == 0x02) { // Bed
        next_state = TEMPERATURE;
      }
      else if (transmission == 0x03) { // Fan Speed
        next_state = TEMPERATURE;
      }
      else if (transmission == 0x04) { // Preheat PLA config
        voice.say(sp3_HEAT);
        voice.say(sp2_P);
        voice.say(sp2_L);
        voice.say(sp2_A);
        next_state = PREHEAT_PLA_CONFIG;
      }
      else if (transmission == 0x05) { // Preheat ABS config
        voice.say(sp3_HEAT);
        voice.say(sp2_A);
        voice.say(sp2_B);
        voice.say(sp2_S);
        next_state = PREHEAT_ABS_CONFIG;
      }
    break;  

    case PREHEAT_PLA_CONFIG: 
      if (transmission == 0x00) {      //temperature
        voice.say(sp3_TEMPERATURE);
        next_state = TEMPERATURE; 
      }
      else if (transmission == 0x01) { // Fan Speed
        next_state = PREHEAT_PLA_CONFIG; 
      }
      else if (transmission == 0x02) { // Nozzle
        next_state = PREHEAT_PLA_CONFIG;
      }
      else if (transmission == 0x03) { // Bed store settings
        voice.say(spt_SAVE);
        next_state = PREHEAT_PLA_CONFIG;
      }
    break;

    case PREHEAT_ABS_CONFIG: 
      if (transmission == 0x00) {      //temperature
        voice.say(sp3_TEMPERATURE);
        next_state = TEMPERATURE; 
      }
      else if (transmission == 0x01) { // Fan Speed 
        next_state = PREHEAT_ABS_CONFIG;
      }
      else if (transmission == 0x02) { // Nozzle
        next_state = PREHEAT_ABS_CONFIG;
      }
      else if (transmission == 0x03) { // Bed store settings
        voice.say(spt_SAVE);
        next_state = PREHEAT_ABS_CONFIG;
      }
    break;

    case MOTION: 
      if (transmission == 0x00) {      //control
        voice.say(sp4_CONTROL); 
        next_state = CONTROL; 
      }
      else if (transmission == 0x01) { //velocity
        voice.say(sp4_SPEED);
        next_state = VELOCITY;
      }
      else if (transmission == 0x02) { //acceleration
        voice.say(sp5_ACCELERATED);
        next_state = ACCELERATION;
      }
      else if (transmission == 0x03) { // jerk
        voice.say(sp2_PULL);
        next_state = JERK;
      }
      else if (transmission == 0x04) { // Steps/mmm
        voice.say(sp3_PER);
        voice.say(sp2_M);
        voice.say(sp2_M);
        next_state = STEPS;
      }
    break;

    case VELOCITY:
      if (transmission == 0x00) {      //Motion
        voice.say(spt_MOVE);
        next_state = MOTION;
      }
      else if (transmission == 0x01) { //Vmax X
        voice.say(sp2_V);
        voice.say(spt_TOP); 
        voice.say(sp2_X);
        next_state = VELOCITY;
      }
      else if (transmission == 0x02) { //Vmax Y
        voice.say(sp2_V);
        voice.say(spt_TOP); 
        voice.say(sp2_Y);
        next_state = VELOCITY;
      }
      else if (transmission == 0x03) { //Vmax Z
        voice.say(sp2_V);
        voice.say(spt_TOP); 
        voice.say(sp2_Z);
        next_state = VELOCITY;
      }
      else if (transmission == 0x04) { //Vmax E
        voice.say(sp2_V);
        voice.say(spt_TOP); 
        voice.say(sp2_E);
        next_state = VELOCITY;
      }
      else if (transmission == 0x05) { //Vmin
        voice.say(sp2_V);
        voice.say(spt_BOTTOM);
        next_state = VELOCITY;
      }
      else if (transmission == 0x06) { //VTrav min
        voice.say(sp2_V);
        voice.say(sp5_FLIGHT);
        voice.say(spt_BOTTOM);
        next_state = VELOCITY;
      }
    break;

    case ACCELERATION: 
      if (transmission == 0x00) {      //Motion
        voice.say(spt_MOVE);
        next_state = MOTION;
      }
      else if (transmission == 0x01) { //Accel
        voice.say(sp5_ACCELERATED);
        next_state = ACCELERATION;
      }
      else if (transmission == 0x02) { //A-retract
        voice.say(sp2_A);
        voice.say(spt_BACK);
        next_state = ACCELERATION;
      }
      else if (transmission == 0x03) { //A-travel
        voice.say(sp2_A);
        voice.say(sp5_FLIGHT);
        next_state = ACCELERATION;
      }
      else if (transmission == 0x04) { //Amax X
        voice.say(sp2_A);
        voice.say(spt_TOP); 
        voice.say(sp2_X);
        next_state = ACCELERATION;
      }
      else if (transmission == 0x05) { //Amax Y
        voice.say(sp2_A);
        voice.say(spt_TOP); 
        voice.say(sp2_Y);
        next_state = ACCELERATION;
      }
      else if (transmission == 0x06) { //Amax Z
        voice.say(sp2_A);
        voice.say(spt_TOP); 
        voice.say(sp2_Z);
        next_state = ACCELERATION;
      }
      else if (transmission == 0x07) { //Amax E
        voice.say(sp2_A);
        voice.say(spt_TOP); 
        voice.say(sp2_E);
        next_state = ACCELERATION;
      }
    break;   

    case JERK: 
      if (transmission == 0x00) {      //Motion
        voice.say(spt_MOVE);
        next_state = MOTION;
      }
      else if (transmission == 0x01) { //Vx-jerk
        voice.say(sp2_V);
        voice.say(sp2_X);
        voice.say(sp2_PULL);
        next_state = JERK;
      }
      else if (transmission == 0x02) { //Vy-jerk
        voice.say(sp2_V);
        voice.say(sp2_Y);
        voice.say(sp2_PULL);
        next_state = JERK;
      }
      else if (transmission == 0x03) { //Vz-jerk
        voice.say(sp2_V);
        voice.say(sp2_Z);
        voice.say(sp2_PULL);
        next_state = JERK;
      }
      else if (transmission == 0x04) { //Ve-jerk
        voice.say(sp2_V);
        voice.say(sp2_E);
        voice.say(sp2_PULL);
        next_state = JERK;
      }
    break; 

    case STEPS: 
      if (transmission == 0x00) {      //Motion
        voice.say(spt_MOVE);
        next_state = MOTION;
      }
      else if (transmission == 0x01) { //Xsteps/mm
        voice.say(sp2_X);
        voice.say(sp3_PER);
        voice.say(sp2_M);
        voice.say(sp2_M);
        next_state = STEPS;
      }
      else if (transmission == 0x02) { //Ysteps/mm
        voice.say(sp2_Y);
        voice.say(sp3_PER);
        voice.say(sp2_M);
        voice.say(sp2_M);
        next_state = STEPS;
      }
      else if (transmission == 0x03) { //Zsteps/mm
        voice.say(sp2_Z);
        voice.say(sp3_PER);
        voice.say(sp2_M);
        voice.say(sp2_M);
        next_state = STEPS;
      }
      else if (transmission == 0x04) { //Esteps/mm
        voice.say(sp2_E);
        voice.say(sp3_PER);
        voice.say(sp2_M);
        voice.say(sp2_M);
        next_state = STEPS;
      }
    break; 

    case NO_TF_CARD: 
      if (transmission == 0x00) {      //info screen
        voice.say(sp4_INFORMATION); 
        next_state = MAIN_MENU;
      }
    break; 

  }
}

void setup() {
  Wire.begin();
  pinMode(buttonTop, INPUT_PULLUP);
  pinMode(buttonSel, INPUT_PULLUP);
  pinMode(buttonBot, INPUT_PULLUP);
  Serial.begin(9600);           // start serial for output
  state_machine(encoderLine, screen_flag);
  Wire.beginTransmission(0x04);
  Wire.write(encoderLine);
  Wire.endTransmission();
  Serial.print(encoderLine);
  Serial.print("\n");
}

void loop() {
  state_machine_top(digitalRead(buttonTop));
  state_machine_sel(digitalRead(buttonSel));
  state_machine_bot(digitalRead(buttonBot));
  delay(20);
  if (buttonTopFlag == 1) {
    encoderLine++; 
    state_machine(encoderLine, screen_flag);
    Wire.beginTransmission(0x04);
    Wire.write(encoderLine);
    Wire.endTransmission();
    Serial.print(encoderLine);
    Serial.print("\n");
  }
  if (buttonSelFlag == 1) {
    encoderLine = 0;
    screen_flag = next_state;
    state_machine(encoderLine, screen_flag);
    Wire.beginTransmission(0x04);
    Wire.write(0xFF);
    Wire.endTransmission();
    Serial.print(0xFF);
    Serial.print("\n");
  }
  if (buttonBotFlag == 1) {
    if (encoderLine != 0) {
      encoderLine--;
    }
      state_machine(encoderLine, screen_flag);
      Wire.beginTransmission(0x04);
      Wire.write(encoderLine);
      Wire.endTransmission();
      Serial.print(encoderLine);
      Serial.print("\n");
  }
}

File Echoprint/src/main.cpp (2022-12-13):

#include "Wire.h"
#include "Arduino.h"
#include "Talkie.h" 
#include "Vocab_US_Large.h"
#include "Vocab_US_TI99.h"

#define I2C_DEV_ADDR 0x04

#define MAIN_MENU 0
#define TUNE 2
#define PREPARE 3
#define CONTROL 4
#define NO_TF_CARD 5
#define BABY_STEP_Z 6
#define PREHEAT_PLA 7
#define PREHEAT_ABS 8
#define MOVE_AXIS 9
#define TEMPERATURE 10
#define MOTION 11
#define PREHEAT_PLA_CONFIG 12
#define PREHEAT_ABS_CONFIG 13
#define VELOCITY 14
#define ACCELERATION 15
#define JERK 16
#define STEPS 17

Talkie voice;
uint32_t i = 0;
byte transmission; 
uint8_t screen_flag = 0; 
uint8_t sel_flag = 0; 


void state_machine(byte transmission, uint8_t screen_flag) {
  
  switch(screen_flag) {
    case MAIN_MENU: 

      if (transmission == 0x00) {      //info screen
        voice.say(sp4_INFORMATION); 
      }
      else if (transmission == 0x01) { //tune
        voice.say(sp2_ADJUST);
      }
      else if (transmission == 0x02) { // prepare
        voice.say(spt_MAKE);
        voice.say(sp4_READY);
      }
      else if (transmission == 0x03) { // control
         voice.say(sp4_CONTROL); 
      }
      else if (transmission == 0x04) { // No TF card
        voice.say(sp4_NO);
        voice.say(sp2_S);
        voice.say(sp2_D);
        voice.say(spt_MEMORY);
      }
      else if (transmission == 0x05) { // init TF card
        voice.say(sp4_START);
        voice.say(sp2_S);
        voice.say(sp2_D);
        voice.say(spt_MEMORY);
      }
      else if (transmission == 0x06) { // About printer
        voice.say(sp2_ABOUT); 
        voice.say(spt_PRINTER); 
      }

    break; 

    case TUNE: 

      if (transmission == 0x00) {      //info screen
        voice.say(sp4_INFORMATION); 
      }
      else if (transmission == 0x01) { //speed
        voice.say(sp4_SPEED);
      }
      else if (transmission == 0x02) { // Nozzle
        
      }
      else if (transmission == 0x03) { // Bed
         
      }
      else if (transmission == 0x04) { // Fan Speed
        
      }
      else if (transmission == 0x05) { // Flow
        voice.say(sp2_FLOW);
      }
      else if (transmission == 0x06) { // Baby step Z
        voice.say(spt_STEP);
        voice.say(sp2_Z);
      }
      else if (transmission == 0x07) { // Change Filament
        voice.say(sp2_CHANGE); 
      }

    break; 
  }

}

void onReceive(int len){
  Serial.printf("onReceive[%d]: ", len);
  while(Wire.available()){
    transmission = Wire.read(); 
    Serial.print(transmission);
    state_machine(transmission, screen_flag);
  }
  Serial.println();
}

void setup() {
  Serial.begin(9600);
  Serial.setDebugOutput(true);
  Wire.onReceive(onReceive);
  Wire.begin((uint8_t)I2C_DEV_ADDR);
 //pinMode(15, OUTPUT); 
  //digitalWrite(27, HIGH);

#if CONFIG_IDF_TARGET_ESP32
  char message[64];
  snprintf(message, 64, "%u Packets.", i++);
  Wire.slaveWrite((uint8_t *)message, strlen(message));
#endif
}

void loop() {

}

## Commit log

2022-12-11 Deleted Talkie Libraries and updated sanguino code with correct pins
    [echoprint_sanguino.ino]
2022-12-11 echoprint .cpp and .h working, printer is sending commands. state machine started on esp32 code
2022-12-13 Just a shit show at this point. Use ESP32 Printer Backup.
2022-12-13 Added CAD Files
    [AXIAL_FAN_COVER.SLDPRT, AXIAL_FAN_COVER.STL, Board_Box.SLDPRT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]
